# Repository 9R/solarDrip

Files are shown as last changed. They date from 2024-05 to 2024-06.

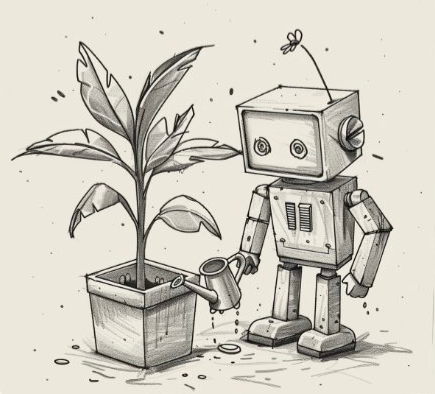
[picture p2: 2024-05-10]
circuit/artwork/dripbot.png

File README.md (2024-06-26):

# SolarDrip

Aim of this project is to create a drop in replacement PCB for low cost solar irrigation systems to allow integration into home automation setups like home-assistant.

## Features

  * solar and usb-c charging
  * basic battery management
  * pump control
  * 2 capacitative sensors (soil & water level)
  * i2c available for additional actors or sensors
  * spare GPIOs

## Hardware

The PCB fits this [solar irrigation system](https://www.aliexpress.com/item/1005006386588305.html). Other, similar systems might be compatible as well. Connecting a pump, 18650 battery and a big enough 6V solar panel should be enough.

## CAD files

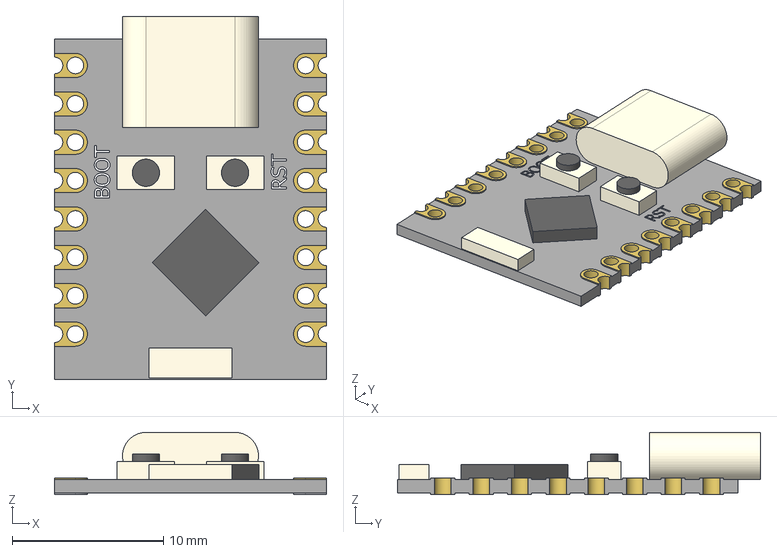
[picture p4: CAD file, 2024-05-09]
circuit/3dmodels/ESP32C3-SuperMini.stp
18.0 x 24.0 x 4.12 mm

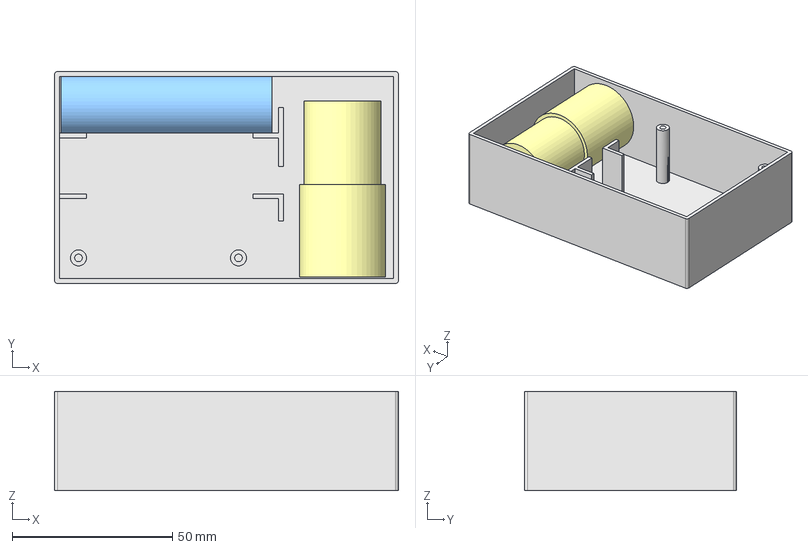
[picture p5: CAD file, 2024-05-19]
mechanical/solarDrip.FCStd
107.5 x 66.2 x 31.0 mm
b_case
b_mount_pcb
b_battery
b_pump

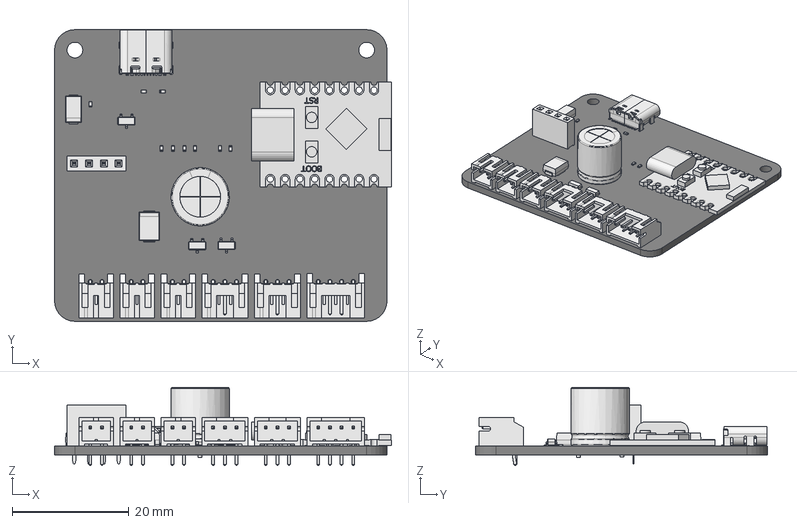
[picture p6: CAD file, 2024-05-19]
mechanical/pcb.FCStd
57.8 x 50.0 x 13.4 mm
Pcb_ad09
Q1_SOT_23_049c3b1e2c4"
Q3_SOT_23_cd7e59cdfb7"
J3_JST_S2B_PH_K_cd6445aa5ba"
J4_JST_S2B_PH_K_c24adcef02a"
D1_D_SMB_2ab0da03007"
USB_C_Receptacle_16P_TopMnt_Horizontal_GCT_USB4105-xx-A
USB_C_Receptacle_16P_TopMnt_Horizontal_GCT_USB4105-xx-A001
USB_C_Receptacle_16P_TopMnt_Horizontal_GCT_USB4105-xx-A002
USB_C_Receptacle_16P_TopMnt_Horizontal_GCT_USB4105-xx-A003
USB_C_Receptacle_16P_TopMnt_Horizontal_GCT_USB4105-xx-A004
USB_C_Receptacle_16P_TopMnt_Horizontal_GCT_USB4105-xx-A005
USB_C_Receptacle_16P_TopMnt_Horizontal_GCT_USB4105-xx-A006
USB_C_Receptacle_16P_TopMnt_Horizontal_GCT_USB4105-xx-A007
USB_C_Receptacle_16P_TopMnt_Horizontal_GCT_USB4105-xx-A008
USB_C_Receptacle_16P_TopMnt_Horizontal_GCT_USB4105-xx-A009
USB_C_Receptacle_16P_TopMnt_Horizontal_GCT_USB4105-xx-A010
USB_C_Receptacle_16P_TopMnt_Horizontal_GCT_USB4105-xx-A011
USB_C_Receptacle_16P_TopMnt_Horizontal_GCT_USB4105-xx-A012
USB_C_Receptacle_16P_TopMnt_Horizontal_GCT_USB4105-xx-A013
USB_C_Receptacle_16P_TopMnt_Horizontal_GCT_USB4105-xx-A014
USB_C_Receptacle_16P_TopMnt_Horizontal_GCT_USB4105-xx-A015
USB_C_Receptacle_16P_TopMnt_Horizontal_GCT_USB4105-xx-A016
USB_C_Receptacle_16P_TopMnt_Horizontal_GCT_USB4105-xx-A017
USB_C_Receptacle_16P_TopMnt_Horizontal_GCT_USB4105-xx-A018
USB_C_Receptacle_16P_TopMnt_Horizontal_GCT_USB4105-xx-A019
USB_C_Receptacle_16P_TopMnt_Horizontal_GCT_USB4105-xx-A020
USB_C_Receptacle_16P_TopMnt_Horizontal_GCT_USB4105-xx-A021
USB_C_Receptacle_16P_TopMnt_Horizontal_GCT_USB4105-xx-A022
USB_C_Receptacle_16P_TopMnt_Horizontal_GCT_USB4105-xx-A023
USB_C_Receptacle_16P_TopMnt_Horizontal_GCT_USB4105-xx-A024
USB_C_Receptacle_16P_TopMnt_Horizontal_GCT_USB4105-xx-A025
USB_C_Receptacle_16P_TopMnt_Horizontal_GCT_USB4105-xx-A026
USB_C_Receptacle_16P_TopMnt_Horizontal_GCT_USB4105-xx-A027
USB_C_Receptacle_16P_TopMnt_Horizontal_GCT_USB4105-xx-A028
USB_C_Receptacle_16P_TopMnt_Horizontal_GCT_USB4105-xx-A029
USB_C_Receptacle_16P_TopMnt_Horizontal_GCT_USB4105-xx-A030
USB_C_Receptacle_16P_TopMnt_Horizontal_GCT_USB4105-xx-A031
USB_C_Receptacle_16P_TopMnt_Horizontal_GCT_USB4105-xx-A032
USB_C_Receptacle_16P_TopMnt_Horizontal_GCT_USB4105-xx-A033
USB_C_Receptacle_16P_TopMnt_Horizontal_GCT_USB4105-xx-A034
USB_C_Receptacle_16P_TopMnt_Horizontal_GCT_USB4105-xx-A035
Q2_SOT_23_4dde82e0f50"
J8_JST_S4B_PH_K_9950e77af00"
D3_D_SMA_43e3f1e46a1"
R2_R_0402_1005Metric_ee0aa82d6d5"
R9_R_0402_1005Metric_65c480be614"
J6_JST_S3B_PH_K_56fc7eee3d2"
C1_CP_Radial_D100mm_P750mm_4415c3f0ead"
R6_R_0402_1005Metric_a7d3baf3f6c"
J2_JST_S2B_PH_K_7740e759bcb"
J1_PinSocket_1x04_P254mm_Vertical_e3e49a1ca17"
R1_R_0402_1005Metric_7fdf6a5df4c"
R5_R_0402_1005Metric_85eb4b1f1d0"
J5_JST_S3B_PH_K_c883a1f1a04"
R4_R_0402_1005Metric_f3baefc1b09"
R3_R_0402_1005Metric_5f29cab19a4"
R7_R_0402_1005Metric_0c1781c3da4"
R8_R_0402_1005Metric_d4f979df027"

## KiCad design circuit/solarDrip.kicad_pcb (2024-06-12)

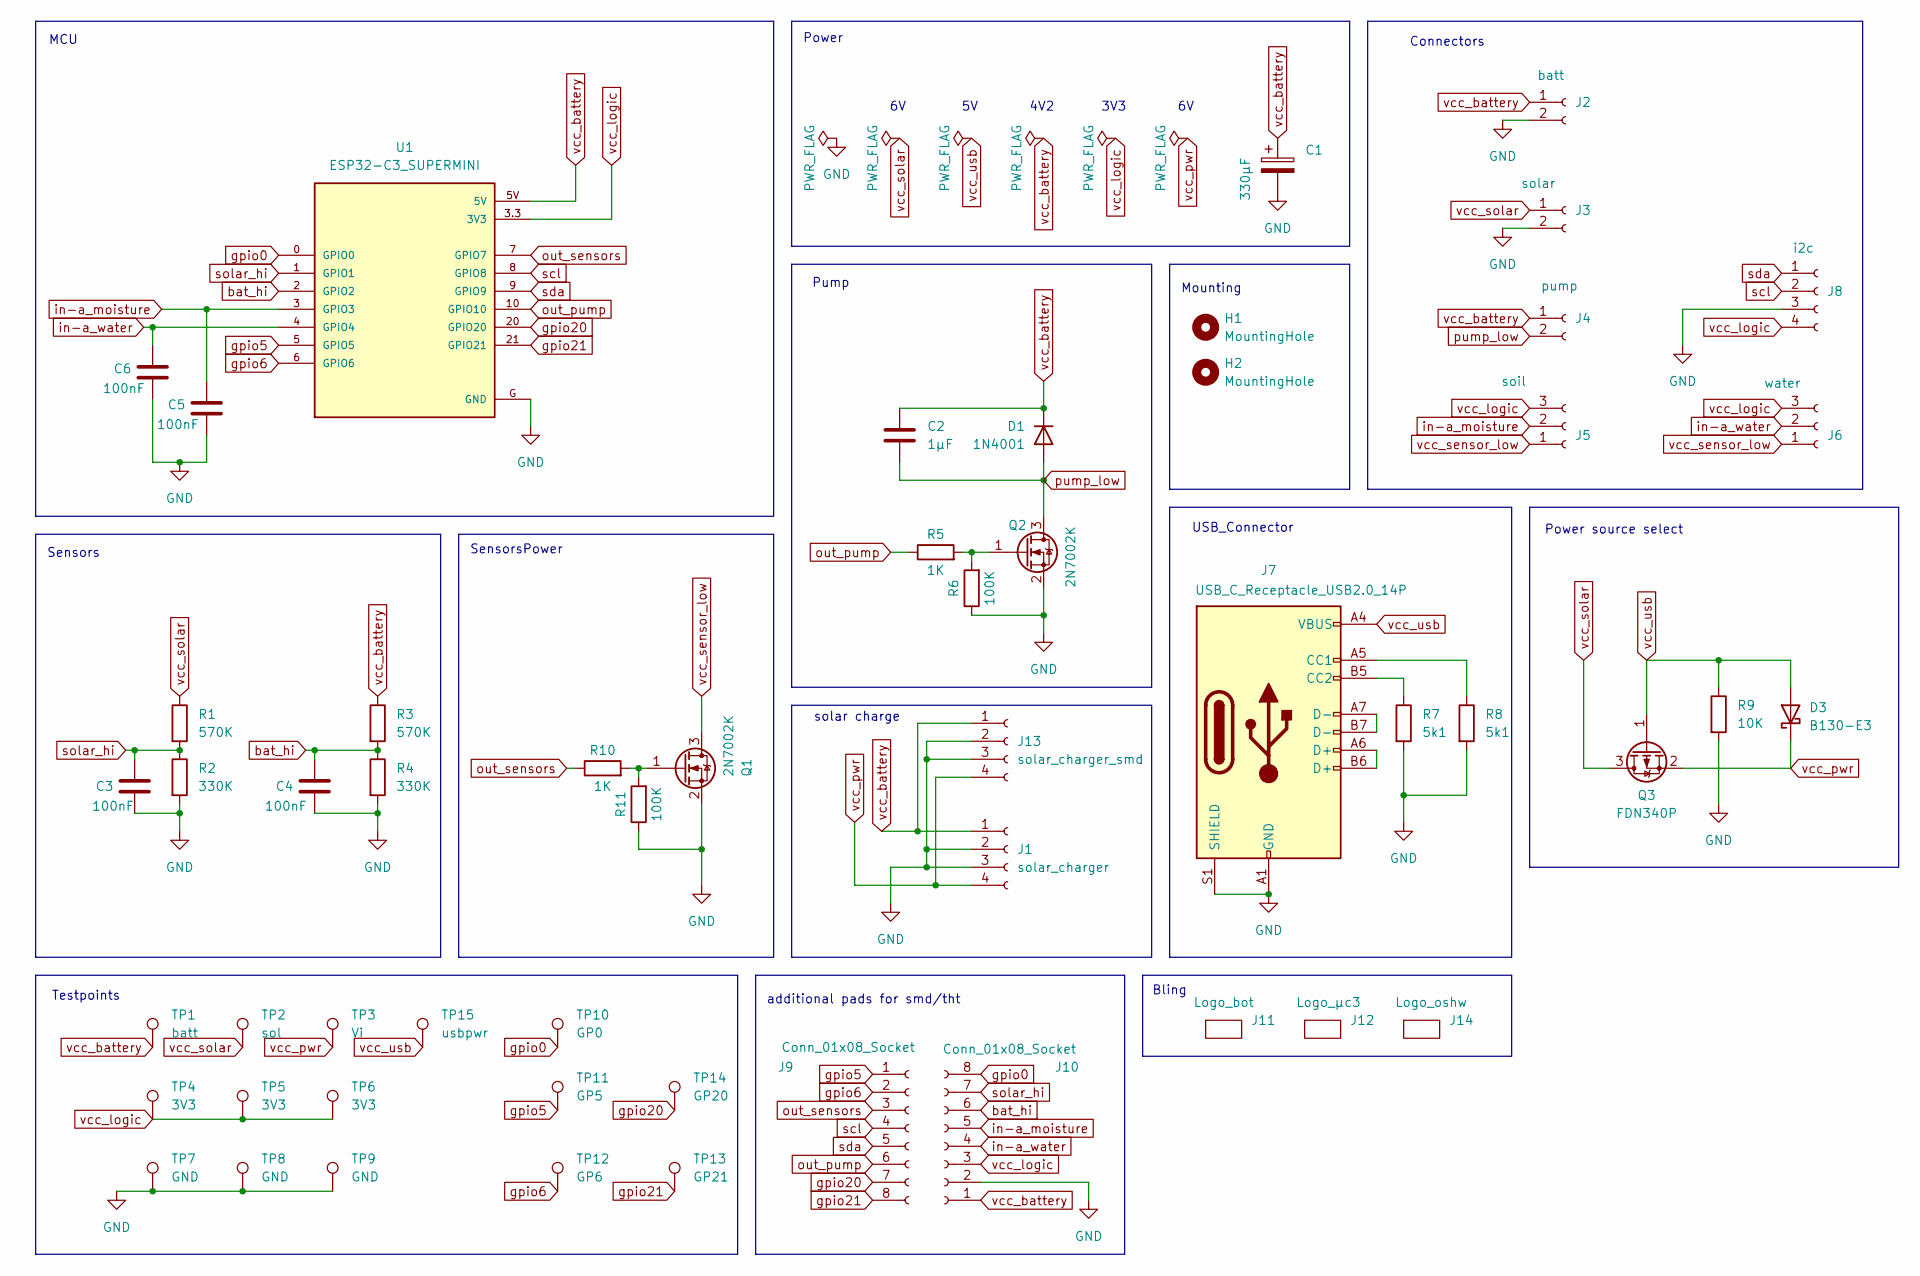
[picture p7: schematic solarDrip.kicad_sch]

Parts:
C1: 330µF; CP_Radial_D8.0mm_P3.80mm
C2: 1µF; C_1206_3216Metric_Pad1.33x1.80mm_HandSolder
C3, C4, C5, C6: 100nF; C_0603_1608Metric_Pad1.08x0.95mm_HandSolder
D1: 1N4001; D_SMA-SMB_Universal_Handsoldering
D3: B130-E3; D_SMA
H1, H2: MountingHole; MountingHole_2.7mm_M2.5_DIN965
J1: solar_charger; PinSocket_1x04_P2.54mm_Vertical
J2: batt; JST_PH_S2B-PH-K_1x02_P2.00mm_Horizontal
J3: solar; JST_PH_S2B-PH-K_1x02_P2.00mm_Horizontal
J4: pump; JST_PH_S2B-PH-K_1x02_P2.00mm_Horizontal
J5: soil; JST_PH_S3B-PH-K_1x03_P2.00mm_Horizontal
J6: water; JST_PH_S3B-PH-K_1x03_P2.00mm_Horizontal
J7: USB_C_Receptacle_USB2.0_14P; USB_C_Receptacle_G-Switch_GT-USB-7010ASV
J8: i2c; JST_PH_S4B-PH-K_1x04_P2.00mm_Horizontal
J9, J10: Conn_01x08_Socket; PinSocket_1x08_P2.54mm_Vertical_SMD_Pin1Left
J11: Logo_bot; logo_solardrip
J12: Logo_µc3; muccc_logo
J13: solar_charger_smd; PinSocket_1x04_P2.54mm_Vertical_SMD_Pin1Left
J14: Logo_oshw; OSHW-Logo_5.7x6mm_SilkScreen
Q1, Q2: 2N7002K; SOT-23
Q3: FDN340P; SOT-23
R1, R3: 570K; R_0603_1608Metric_Pad0.98x0.95mm_HandSolder
R2, R4: 330K; R_0603_1608Metric_Pad0.98x0.95mm_HandSolder
R5, R10: 1K; R_0603_1608Metric_Pad0.98x0.95mm_HandSolder
R6, R11: 100K; R_0603_1608Metric_Pad0.98x0.95mm_HandSolder
R7, R8: 5k1; R_0603_1608Metric_Pad0.98x0.95mm_HandSolder
R9: 10K; R_0603_1608Metric_Pad0.98x0.95mm_HandSolder
TP1: batt; TestPoint_Pad_D2.0mm
TP2: sol; TestPoint_Pad_D2.0mm
TP3: Vi; TestPoint_Pad_D2.0mm
TP4, TP5, TP6: 3V3; TestPoint_Pad_D2.0mm
TP7, TP8, TP9: GND; TestPoint_Pad_2.0x2.0mm
TP10: GP0; TestPoint_Pad_D2.0mm
TP11: GP5; TestPoint_Pad_D2.0mm
TP12: GP6; TestPoint_Pad_D2.0mm
TP13: GP21; TestPoint_Pad_D2.0mm
TP14: GP20; TestPoint_Pad_D2.0mm
TP15: usbpwr; TestPoint_Pad_D2.0mm
U1: ESP32-C3_SUPERMINI; MODULE_ESP32-C3_SUPERMINI

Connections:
GND: C1.2, C3.2, C4.2, C5.2, C6.2, J1.2, J1.3, J2.2, J3.2, J7.A1 (GND), J7.A12 (GND), J7.B1 (GND), J7.B12 (GND), J7.S1 (SHIELD), J8.3, J10.2, J13.2, J13.3, Q1.2 (S), Q2.2 (S), R2.2, R4.2, R6.1, R7.2, R8.2, R9.2, R11.1, TP7.1, TP8.1, TP9.1, U1.G (GND)
unnamed: J7.A5 (CC1), R8.1
unnamed: J7.B5 (CC2), R7.1
unnamed: J7.A6 (D+), J7.B6 (D+)
unnamed: J7.A7 (D-), J7.B7 (D-)
unnamed: Q1.1 (G), R10.2, R11.2
unnamed: Q2.1 (G), R5.2, R6.2
bat_hi: C4.1, J10.6, R3.2, R4.1, U1.2 (GPIO2)
gpio0: J10.8, TP10.1, U1.0 (GPIO0)
gpio5: J9.1, TP11.1, U1.5 (GPIO5)
gpio6: J9.2, TP12.1, U1.6 (GPIO6)
gpio20: J9.7, TP14.1, U1.20 (GPIO20)
gpio21: J9.8, TP13.1, U1.21 (GPIO21)
in-a_moisture: C5.1, J5.2, J10.5, U1.3 (GPIO3)
in-a_water: C6.1, J6.2, J10.4, U1.4 (GPIO4)
out_pump: J9.6, R5.1, U1.10 (GPIO10)
out_sensors: J9.3, R10.1, U1.7 (GPIO7)
pump_low: C2.2, D1.2 (A), J4.2, Q2.3 (D)
scl: J8.2, J9.4, U1.8 (GPIO8)
sda: J8.1, J9.5, U1.9 (GPIO9)
solar_hi: C3.1, J10.7, R1.2, R2.1, U1.1 (GPIO1)
vcc_battery: C1.1, C2.1, D1.1 (K), J1.1, J2.1, J4.1, J10.1, J13.1, R3.1, TP1.1, U1.5V
vcc_logic: J5.3, J6.3, J8.4, J10.3, TP4.1, TP5.1, TP6.1, U1.3.3 (3V3)
vcc_pwr: D3.1 (K), J1.4, J13.4, Q3.2 (S), TP3.1
vcc_sensor_low: J5.1, J6.1, Q1.3 (D)
vcc_solar: J3.1, Q3.3 (D), R1.1, TP2.1
vcc_usb: D3.2 (A), J7.A4 (VBUS), J7.A9 (VBUS), J7.B4 (VBUS), J7.B9 (VBUS), Q3.1 (G), R9.1, TP15.1

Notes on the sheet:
Power source select
Bling
Mounting
3V3
MCU
SensorsPower
Connectors
USB_Connector
solar charge
4V2
Testpoints
Pump
Power
additional pads for smd/tht
Sensors

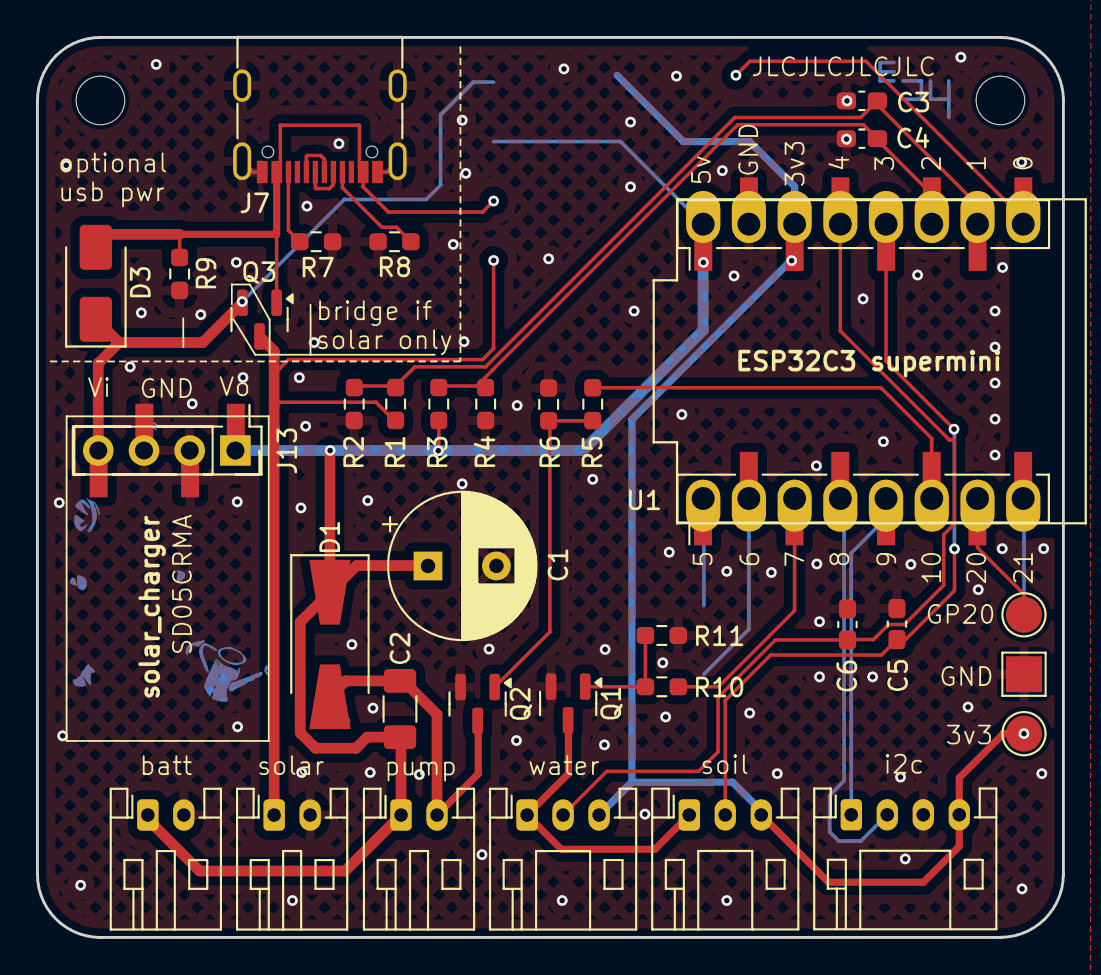
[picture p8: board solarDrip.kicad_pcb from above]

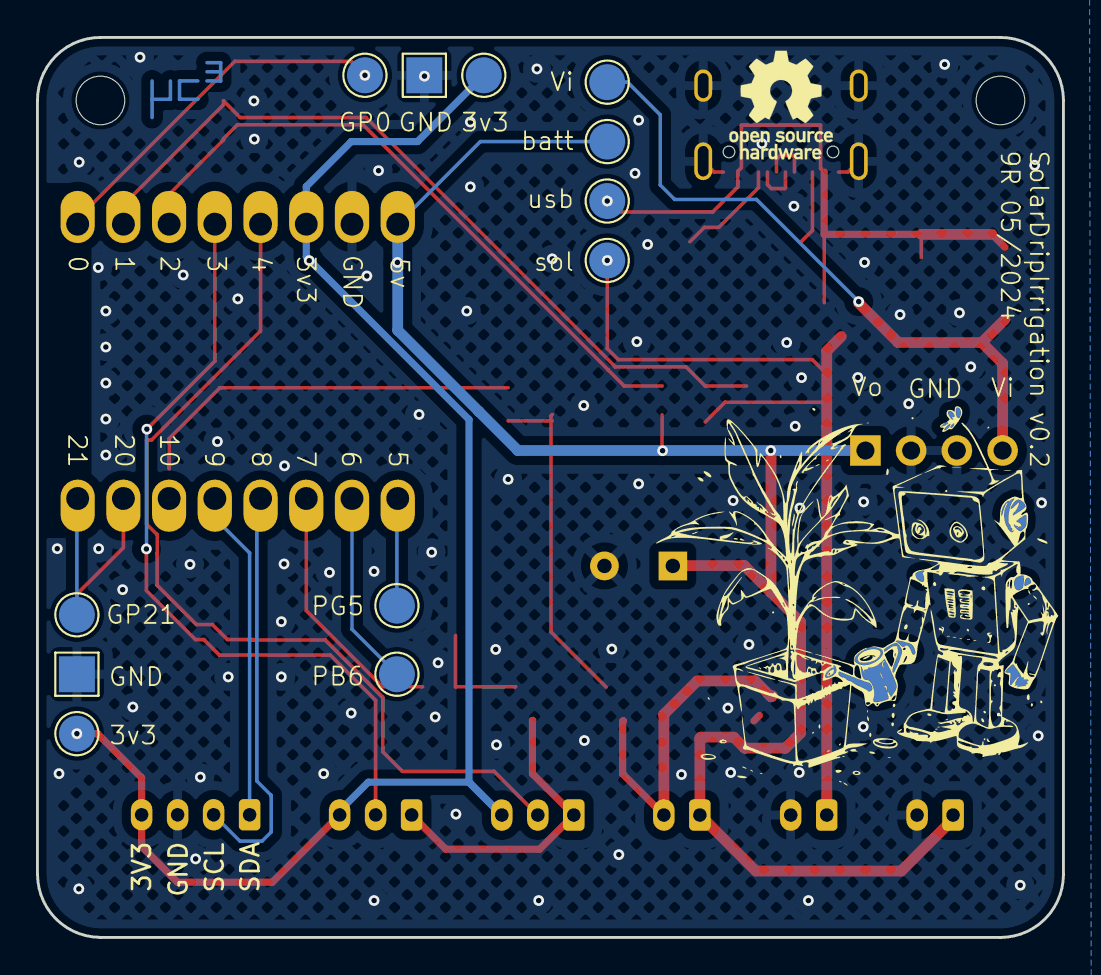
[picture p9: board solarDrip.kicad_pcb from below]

Board: 2 copper layers, 57.0 x 50.0 mm, 54 parts (15 on the bottom side), 27 nets.

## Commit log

2024-05-01 add mechanical model
    [solarDrip.FCStd]
2024-05-01 add pcb to mechanical model
    [pcb.FCStd, solarDrip.FCStd]
2024-05-01 prepare pcb for edge import
    [solarDrip.kicad_pcb, solarDrip.kicad_sch]
2024-05-03 add usb charging source
    [solarDrip.kicad_pcb, solarDrip.kicad_sch]
2024-05-03 cleanup and annotations
    [solarDrip.kicad_sch]
2024-05-03 replace usb_connector
    [solarDrip.kicad_sch]
2024-05-03 various updates
    [solarDrip.kicad_pcb, solarDrip.kicad_sch]
2024-05-03 add esp32c3 supermini 3d model
2024-05-03 update pcb model
    [pcb.FCStd, solarDrip.FCStd]
2024-05-08 add s annotations
    [solarDrip.kicad_sch]
2024-05-09 init supermini variant
    [ESP32C3-SuperMini.stp, pcb.FCStd, solarDrip.FCStd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]
2024-05-09 add usb_charging
    [solarDrip.kicad_sch]
2024-05-09 add power select circuit
    [solarDrip.kicad_sch]
2024-05-09 first stab at pcb placement
    [solarDrip.kicad_pcb, solarDrip.kicad_sch]
2024-05-09 routing done
    [solarDrip.kicad_pcb]
2024-05-09 run drc
    [solarDrip.kicad_pcb]
2024-05-09 add testpoints & i2c to scematics
    [solarDrip.kicad_sch]
2024-05-09 vias, silkscreen, add usb_prw, logos and serials
    [solarDrip.kicad_pcb, solarDrip.kicad_sch]
2024-05-09 flip usb and testpoint sides
    [solarDrip.kicad_pcb]
2024-05-09 add capacitor, cleanup
    [solarDrip.kicad_pcb, solarDrip.kicad_sch]
2024-05-10 move usb_pwr parts around
    [solarDrip.kicad_pcb]
2024-05-10 move more stuff around
    [solarDrip.kicad_pcb]
2024-05-10 add motor cap
    [solarDrip.kicad_pcb, solarDrip.kicad_sch]
2024-05-14 add additional pads for smd/tht sockets
    [solarDrip.kicad_sch]
2024-05-14 pcb: add U1 smd pads
    [solarDrip.kicad_pcb, solarDrip.kicad_sch]
2024-05-14 sch: add bypass caps to sensor pins
    [solarDrip.kicad_sch]
2024-05-14 add sensor pypass caps
    [solarDrip.kicad_pcb, solarDrip.kicad_sch]
2024-05-14 add artwork: dripbot & mc3 logo
    [solarDrip.kicad_pcb, solarDrip.kicad_sch]
2024-05-19 add knockout fonts
    [solarDrip.kicad_pcb, solarDrip.kicad_sch]
2024-05-19 update mechanical model
    [pcb.FCStd, solarDrip.FCStd]
2024-05-19 add hatched fill
    [solarDrip.kicad_pcb]
2024-05-20 check vias
    [solarDrip.kicad_pcb]
2024-05-20 resize R1-R4 to 0306
    [solarDrip.kicad_pcb, solarDrip.kicad_sch]
2024-05-20 resize R5-R9 to 0306
    [solarDrip.kicad_pcb, solarDrip.kicad_sch]
2024-05-20 add logo symbols
    [solarDrip.kicad_pcb, solarDrip.kicad_sch]
2024-05-20 fix usb net
    [solarDrip.kicad_pcb, solarDrip.kicad_sch]
2024-05-20 add OSHW logo
    [solarDrip.kicad_sch]
2024-05-20 small improvements
    [solarDrip.kicad_pcb]
2024-05-20 change caps to 0603
    [solarDrip.kicad_pcb, solarDrip.kicad_sch]
2024-05-22 set resistor values, schematic cleanup
    [solarDrip.kicad_pcb, solarDrip.kicad_sch]
2024-05-24 set R values
    [solarDrip.kicad_pcb]
2024-05-26 minor postioning adjustments
    [solarDrip.kicad_pcb]
2024-06-12 v0.1 production layout
    [solarDrip.kicad_pcb]
